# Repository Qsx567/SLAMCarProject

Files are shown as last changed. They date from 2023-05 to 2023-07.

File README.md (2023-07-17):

# SLAMCarProject
### 本项目为我设计的移动SLAM机器人，命名为： <font face="Times New Roman">Q-Robot</font>
<div align="center">
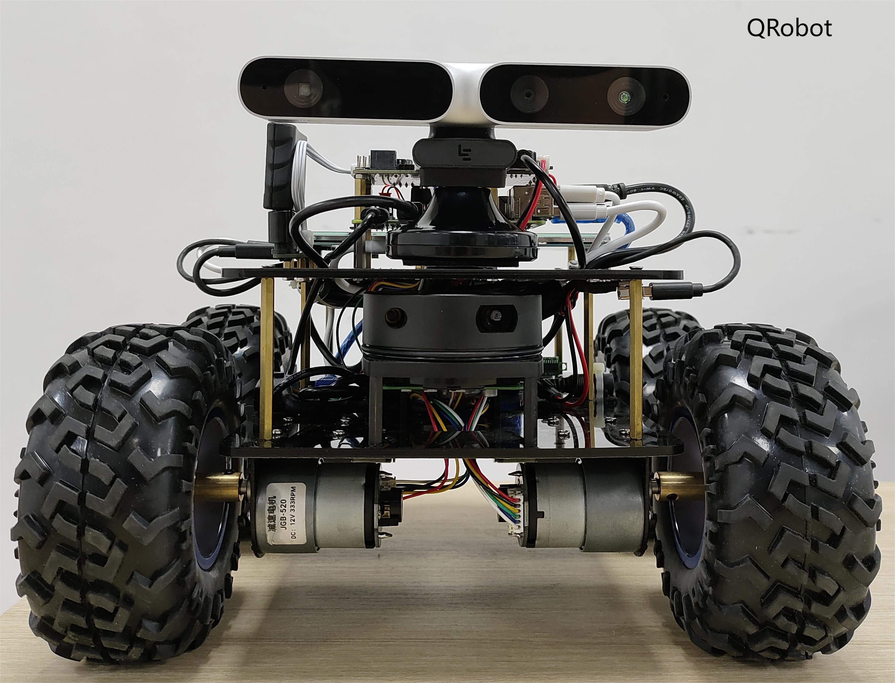
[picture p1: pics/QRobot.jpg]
    <br>
    <font color=#a0a0a0 size=2> 第一层亚克力板图纸</font>
</div>
- 机器人底盘控制器：**STM32F103RCT6**
- 上层控制器：**树莓派4B**
- 传感器：
  - 思岚A1激光雷达
  - Orbbec Astra Pro RGB-D相机
  - 高精度9轴惯导模块N100
  - PS2遥控器
  - wheeltec手柄
- 软件：
  - STM32CubeMX 6.7.0
  - Keil 5.29.0
  - 立创EDA
  - CAD迷你画图

## 一、机器人底盘（亚克力板图纸）
- 总共包括两个文件(plate->plate1.dwg/plate2.dwg)
  - 第一层亚克力板图纸（可放置520电机、锂电池、思岚A1激光雷达/串口板）
  - 第二层亚克力板图纸（可放置Orbbec Astra Pro RGB-D相机、树莓派4B、STM32控制板、PS2遥控器接收器、7寸的显示屏）

<div align="center">
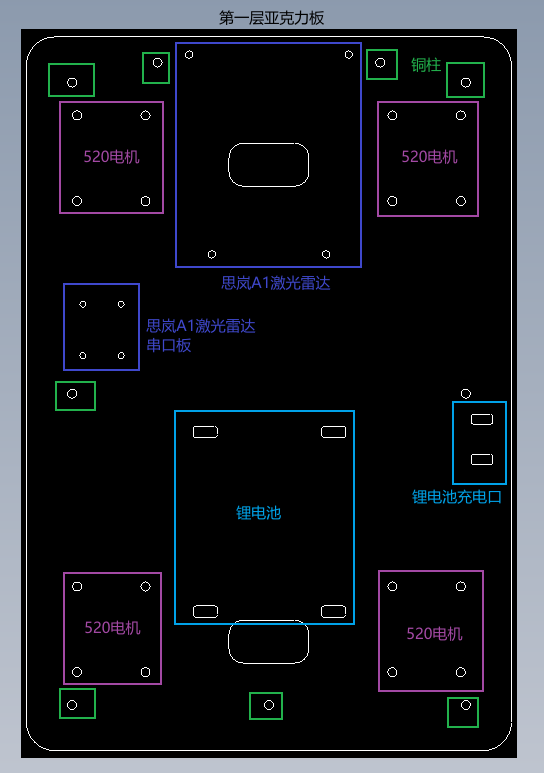
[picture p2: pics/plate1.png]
    <br>
    <font color=#a0a0a0 size=2> 第一层亚克力板图纸</font>
</div>

<div align="center">
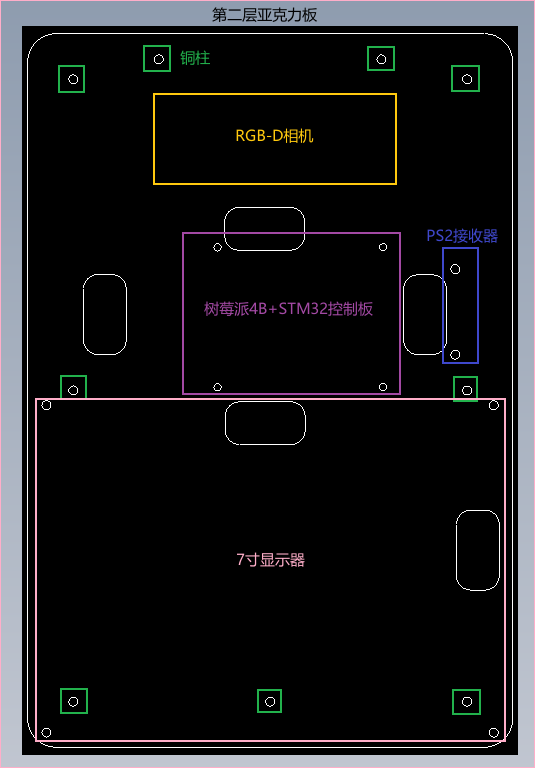
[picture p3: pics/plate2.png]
    <br>
    <font color=#a0a0a0 size=2> 第二层亚克力板图纸</font>
</div>

## 二、机器人底盘控制器原理图

<div align="center">
    <br>
    <font color=#a0a0a0 size=2> 基于SMT32F103RCT6的控制器原理图</font>
</div>

## 三、机器人底盘控制器PCB图

<div align="center">
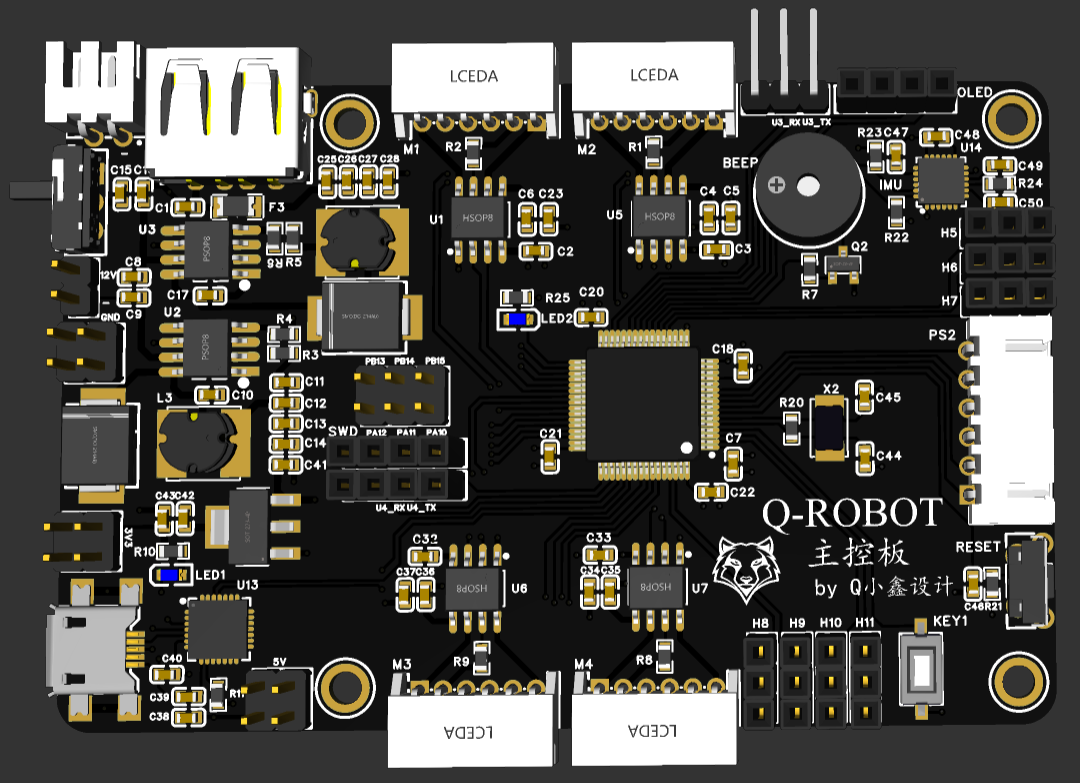
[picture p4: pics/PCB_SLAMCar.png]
    <br>
    <font color=#a0a0a0 size=2> 基于SMT32F103RCT6的控制器PCB图</font>
</div>

## 四、机器人底盘控制器--> STM32
- 电机控制（motor）:TIM5/TIM8
  - Motor1：TIM8_CH1/TIM8_CH2
  - Motor2：TIM5_CH3/TIM5_CH4
  - Motor3：TIM8_CH3/TIM8_CH4
  - Motor4：TIM5_CH1/TIM8_CH2
- 编码器（Encoder）：TIM1/TIM2/TIM3/TIM4
  - Encoder1:TIM1
  - Encoder2:TIM2
  - Encoder3:TIM3
  - Encoder4:TIM4
- PS2遥控器
  - PC0 ->Input    PS2_DAT
  - PC1 ->Output   PS2_COM
  - PC2 ->Output   PS2_ATT
  - PC3 ->OutPut   PS2_CLK
- 串口（UART5）
  - PD2  --> U5_RX
  - PC12 --> U5_TX
- MPU6050（IIC）
  - MPU6050_SDA：PC4
  - MPU6050_SCL：PC5
## 五、ROS相关教程
- 1.使用思岚A1激光雷达
  - 链接: [ROS下使用激光雷达](https://blog.csdn.net/qq_42108414/article/details/121065197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)
- 2.使用Wheeltec N100惯性模块
  - 链接: [ROS下使用N100模块](https://qiushuxin.blog.csdn.net/article/details/130932265)
- 3.使用乐视深度相机LeTMC-520
  - 链接: [ROS下使用乐视深度相机LeTMC-520](https://qiushuxin.blog.csdn.net/article/details/130940896)

已完成情况：
- [x]  添加电机控制（PWM）相关代码
- [x]  添加编码器数据的采集以及转化为速度m/s
- [x]  添加机器人运动模型（四轮模型）运动学逆解
- [x]  添加PID控制算法（增量式） 
- [x]  添加PS2遥控器相关代码
- [x]  添加MPU6050驱动代码，可获取加速度原始值和角速度原始值
- [x]  添加将底层控制数据通过串口发送给ROS端
- [x]  新增FreeRTOS功能，后续只修改维护QRobot_FreeRTOS，基本功能和无OS版本一致，不同之处只是一些逻辑方面
- [x]  添加OLED驱动程序
- [x]  增加思岚A1激光雷达驱动代码
- [x]  增加N100惯性导航模块驱动代码 
- [x]  增加乐视深度相机LeTMC-520驱动代码  
- [x]  增加wheeltec手柄的驱动代码
- [x]  增加STM32和ROS串口通信代码
- [x]  增加PID动态调参代码

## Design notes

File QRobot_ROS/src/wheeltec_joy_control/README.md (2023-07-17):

# 轮趣的PS2遥控器使用方法

## 1、查看输入
```
ls /dev/input
```

## 2、测试
```
sudo apt-get install joystick
sudo jstest /dev/input/js0
```

## 3、编译功能包
```
catkin_make -DCATKIN_WHITELIST_PACKAGES="wheeltec_joy_control"
roslaunch wheeltec_joy joy_data.launch
```

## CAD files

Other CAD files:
plate/plate1.dwg
plate/plate2.dwg

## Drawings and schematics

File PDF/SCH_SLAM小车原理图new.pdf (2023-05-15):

## 电机/编码器接口

## 晶振电路

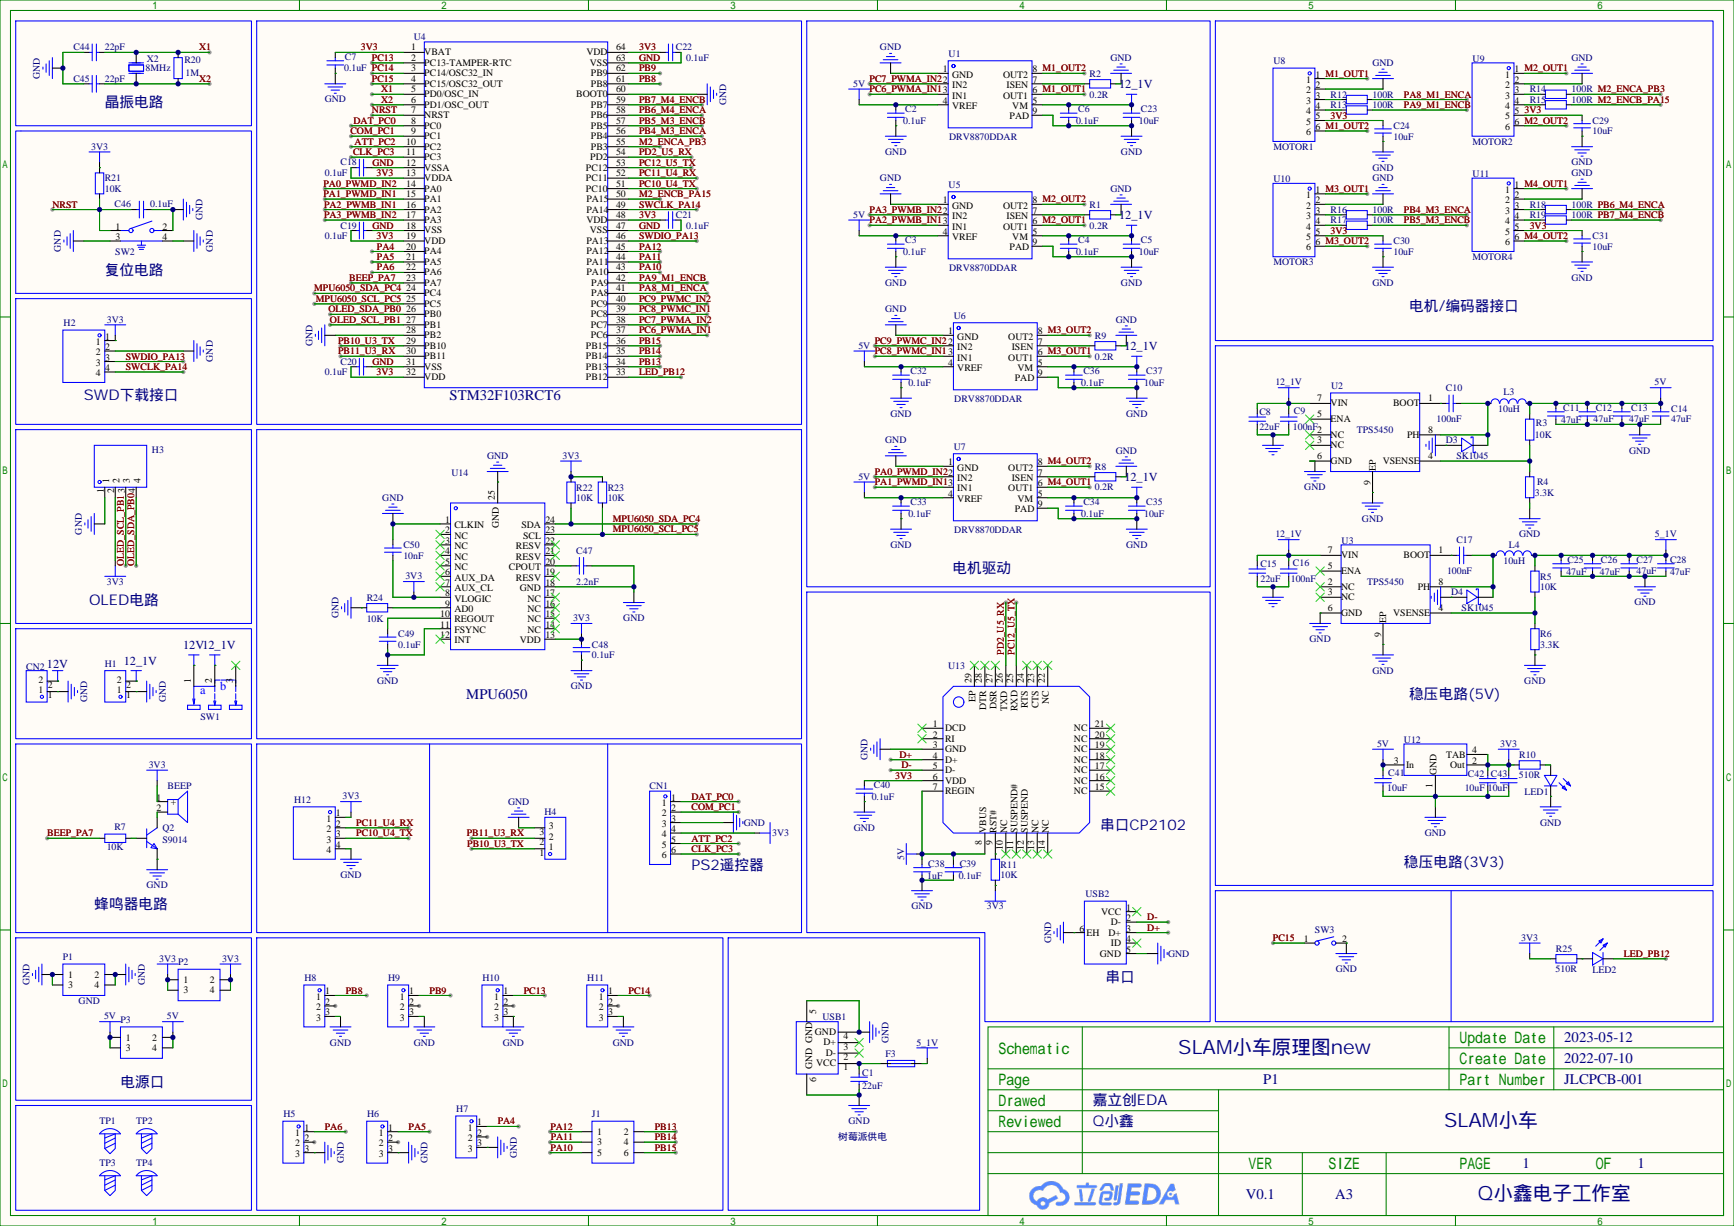
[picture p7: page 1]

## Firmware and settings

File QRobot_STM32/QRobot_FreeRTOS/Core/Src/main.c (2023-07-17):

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
/* Includes ------------------------------------------------------------------*/
#include "main.h"
#include "cmsis_os.h"
#include "tim.h"
#include "usart.h"
#include "gpio.h"


void SystemClock_Config(void);
void MX_FREERTOS_Init(void);
/**
  * @brief  The application entry point.
  * @retval int
  */
int main(void)
{
  /* MCU Configuration--------------------------------------------------------*/

  /* Reset of all peripherals, Initializes the Flash interface and the Systick. */
  HAL_Init();

  /* Configure the system clock */
  SystemClock_Config();

  /* Initialize all configured peripherals */
  MX_GPIO_Init();
  MX_TIM5_Init();
  MX_TIM8_Init();
  MX_TIM1_Init();
  MX_TIM2_Init();
  MX_TIM3_Init();
  MX_TIM4_Init();
  MX_UART5_Init();
  /* USER CODE BEGIN 2 */
	
	OLED_Init();//OLED初始化
	
//	OLED_Refresh();
	
	PS2_Init(); //PS2手柄初始化
	MPU6050_Init(); // MPU6050初始化
	// 电机PWM，满占空比是7199
	HAL_TIM_PWM_Start(&htim8, TIM_CHANNEL_1); // M1_PWMA_1
	HAL_TIM_PWM_Start(&htim8, TIM_CHANNEL_2); // M1_PWMA_2
	HAL_TIM_PWM_Start(&htim8, TIM_CHANNEL_3); // M3_PWMA_1
	HAL_TIM_PWM_Start(&htim8, TIM_CHANNEL_4); // M3_PWMA_2
	
	HAL_TIM_PWM_Start(&htim5, TIM_CHANNEL_1); // M4_PWMA_1
	HAL_TIM_PWM_Start(&htim5, TIM_CHANNEL_2); // M4_PWMA_2
	HAL_TIM_PWM_Start(&htim5, TIM_CHANNEL_3); // M2_PWMA_1
	HAL_TIM_PWM_Start(&htim5, TIM_CHANNEL_4); // M2_PWMA_2
	
	// 编码器
	HAL_TIM_Encoder_Start(&htim1,TIM_CHANNEL_ALL); // M1_ENC
	HAL_TIM_Encoder_Start(&htim2,TIM_CHANNEL_ALL); // M2_ENC
	HAL_TIM_Encoder_Start(&htim3,TIM_CHANNEL_ALL); // M3_ENC
	HAL_TIM_Encoder_Start(&htim4,TIM_CHANNEL_ALL); // M4_ENC
	
	// 串口
	HAL_UART_Receive_IT(&huart5,(void *)&uart5_rxbuff,1);
  /* USER CODE END 2 */

  /* Call init function for freertos objects (in freertos.c) */
  MX_FREERTOS_Init();

  /* Start scheduler */
  osKernelStart();

  /* We should never get here as control is now taken by the scheduler */
  /* Infinite loop */
  /* USER CODE BEGIN WHILE */
  while (1)
  {

		
		
    /* USER CODE END WHILE */

    /* USER CODE BEGIN 3 */
  }
  /* USER CODE END 3 */
}

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
/**
  * @brief  Period elapsed callback in non blocking mode
  * @note   This function is called  when TIM6 interrupt took place, inside
  * HAL_TIM_IRQHandler(). It makes a direct call to HAL_IncTick() to increment
  * a global variable "uwTick" used as application time base.
  * @param  htim : TIM handle
  * @retval None
  */
void HAL_TIM_PeriodElapsedCallback(TIM_HandleTypeDef *htim)
{
  if (htim->Instance == TIM6) {
    HAL_IncTick();
  }
}

/**
  * @brief  This function is executed in case of error occurrence.
  * @retval None
  */
void Error_Handler(void)
{
  /* USER CODE BEGIN Error_Handler_Debug */
  /* User can add his own implementation to report the HAL error return state */
  __disable_irq();
  while (1)
  {
  }
  /* USER CODE END Error_Handler_Debug */
}

#ifdef  USE_FULL_ASSERT
/**
  * @brief  Reports the name of the source file and the source line number
  *         where the assert_param error has occurred.
  * @param  file: pointer to the source file name
  * @param  line: assert_param error line source number
  * @retval None
  */
void assert_failed(uint8_t *file, uint32_t line)
{
  /* USER CODE BEGIN 6 */
  /* User can add his own implementation to report the file name and line number,
     ex: printf("Wrong parameters value: file %s on line %d\r\n", file, line) */
  /* USER CODE END 6 */
}
#endif /* USE_FULL_ASSERT */

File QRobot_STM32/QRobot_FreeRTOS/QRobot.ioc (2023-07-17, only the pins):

Mcu.UserName=STM32F103RCTx
PA0-WKUP.Signal=S_TIM5_CH1
PA1.Signal=S_TIM5_CH2
PA13.Signal=SYS_JTMS-SWDIO
PA14.Signal=SYS_JTCK-SWCLK
PA15.Signal=S_TIM2_CH1_ETR
PA2.Signal=S_TIM5_CH3
PA3.Signal=S_TIM5_CH4
PA7.GPIO_Label=BEEP
PA7.Signal=GPIO_Output
PA8.Signal=S_TIM1_CH1
PA9.Signal=S_TIM1_CH2
PB0.GPIO_Label=OLED_SDA
PB0.Signal=GPIO_Output
PB1.GPIO_Label=OLED_SCL
PB1.Signal=GPIO_Output
PB12.GPIO_Label=LED
PB12.Signal=GPIO_Output
PB3.Signal=S_TIM2_CH2
PB4.Signal=S_TIM3_CH1
PB5.Signal=S_TIM3_CH2
PB6.Signal=S_TIM4_CH1
PB7.Signal=S_TIM4_CH2
PC0.GPIO_Label=PS2_DAT
PC0.Signal=GPIO_Input
PC1.GPIO_Label=PS2_COM
PC1.Signal=GPIO_Output
PC12.Signal=UART5_TX
PC15-OSC32_OUT.GPIO_Label=KEY
PC15-OSC32_OUT.Signal=GPIO_Input
PC2.GPIO_Label=PS2_ATT
PC2.Signal=GPIO_Output
PC3.GPIO_Label=PS2_CLK
PC3.Signal=GPIO_Output
PC4.GPIO_Label=MPU6050_SDA
PC4.Signal=GPIO_Output
PC5.GPIO_Label=MPU6050_SCL
PC5.Signal=GPIO_Output
PC6.Signal=S_TIM8_CH1
PC7.Signal=S_TIM8_CH2
PC8.Signal=S_TIM8_CH3
PC9.Signal=S_TIM8_CH4
PD0-OSC_IN.Signal=RCC_OSC_IN
PD1-OSC_OUT.Signal=RCC_OSC_OUT
PD2.Signal=UART5_RX

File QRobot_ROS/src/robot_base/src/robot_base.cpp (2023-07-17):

#include "robot_base.h"

using namespace std;

float Robot_base::KP = 0;
float Robot_base::KI = 0;
float Robot_base::KD = 0;

// 构造函数
Robot_base::Robot_base()
{
    // 清空接发数据
    memset(&Reciver_Str,0,sizeof(Reciver_Str));
    memset(&Send_Str,0,sizeof(Send_Str));
    x = y = th = vx = vth = dt = 0.0;   

    //发送串口的包头和包尾
    Send_Str.Sensor_str.Header = RECIVER_DATA_HEADER;
    Send_Str.Sensor_str.End = RECIVER_DATA_END;
 
    // 加载串口参数
    nh.param<std::string>("serial/usart_port", this->usart_port, "/dev/ttyUSB0"); // 设置串口端口
    nh.param<int>("serial/baud_rate", this->baud_rate, 115200); // 设置波特率

    // 加载PID参数
    nh.param<float>("PID/KP", Robot_base::KP, 0.0);
    nh.param<float>("PID/KI", Robot_base::KI, 0.0);
    nh.param<float>("PID/KD", Robot_base::KD, 0.0);
    ROS_INFO("KP KI KD = [%f,%f,%f]",Robot_base::KP,Robot_base::KI,Robot_base::KD);
    // 发布话题
    this->moto_pub = nh.advertise<std_msgs::Float32MultiArray>("/robot/MotoEnder",30);
    this->odom_pub = nh.advertise<nav_msgs::Odometry>("odom",50);

    // 订阅话题
    this->cmd_vel_sub = nh.subscribe("/cmd_vel", 100, &Robot_base::cmd_velCallback, this);


    // 创建PID动态参数服务器
    // f = boost::bind(&Robot_base::dynamicParamCallback,_1);
    // server.setCallback(f);
    


    // 打开串口
    try{
        Robot_serial.setPort(this->usart_port);
        Robot_serial.setBaudrate(this->baud_rate);
        serial::Timeout to = serial::Timeout::simpleTimeout(1000);//设置串口超时时间
        Robot_serial.setTimeout(to);
        Robot_serial.open();//打开串口
    }
    catch(serial::IOException &e){
        ROS_INFO_STREAM("Failed to open port ");
    }
    if(Robot_serial.isOpen()){
        ROS_INFO_STREAM("Serial Port initialized!");
    }
    else{
        ROS_INFO_STREAM("Failed to open port ");
    }


}

Robot_base::~Robot_base()
{
    Robot_serial.close();//关闭串口
    cout << "over!!!" <<endl;
}

// 串口读取函数`
bool Robot_base::ReadUart()
{
    unsigned char CheckSumBuffer[1]; 
    Robot_serial.read(Reciver_Str.buffer,sizeof(Reciver_Str.buffer));
    if(Reciver_Str.Sensor_str.Header == RECIVER_DATA_HEADER){
        if(Reciver_Str.Sensor_str.End == RECIVER_DATA_END){
            
            // 获得机器人的速度值
            this->vx  = Reciver_Str.Sensor_str.X_speed;
            this->vth = Reciver_Str.Sensor_str.Z_speed;

            // 获得加速度和角速度值
            MPU6050.linear_acceleration.x = Reciver_Str.Sensor_str.Accelerometer.X_data / ACCELEROMETER;
            MPU6050.linear_acceleration.y = Reciver_Str.Sensor_str.Accelerometer.Y_data / ACCELEROMETER;
            MPU6050.linear_acceleration.z = Reciver_Str.Sensor_str.Accelerometer.Z_data / ACCELEROMETER;

            MPU6050.angular_velocity.x = Reciver_Str.Sensor_str.Gyroscope.X_data * GYROSCOPE_RADIAN;
            MPU6050.angular_velocity.y = Reciver_Str.Sensor_str.Gyroscope.Y_data * GYROSCOPE_RADIAN;
            MPU6050.angular_velocity.z = Reciver_Str.Sensor_str.Gyroscope.Z_data * GYROSCOPE_RADIAN;

            return true;
        }
    }
    //读取空字节防止卡死
    Robot_serial.read(CheckSumBuffer,sizeof(CheckSumBuffer));
    return false;
}

// 发布编码器速度值话题
void Robot_base::PublisherMotoEncoder()
{
    //M1
    Moto_Str.data.push_back(Reciver_Str.Sensor_str.MotoStr[0].Moto_CurrentSpeed);
    Moto_Str.data.push_back(Reciver_Str.Sensor_str.MotoStr[0].Moto_TargetSpeed);

    //M2
    Moto_Str.data.push_back(Reciver_Str.Sensor_str.MotoStr[1].Moto_CurrentSpeed);
    Moto_Str.data.push_back(Reciver_Str.Sensor_str.MotoStr[1].Moto_TargetSpeed);

    //M3
    Moto_Str.data.push_back(Reciver_Str.Sensor_str.MotoStr[2].Moto_CurrentSpeed);
    Moto_Str.data.push_back(Reciver_Str.Sensor_str.MotoStr[2].Moto_TargetSpeed);

    //M3
    Moto_Str.data.push_back(Reciver_Str.Sensor_str.MotoStr[3].Moto_CurrentSpeed);
    Moto_Str.data.push_back(Reciver_Str.Sensor_str.MotoStr[3].Moto_TargetSpeed);

    //M4
    Moto_Str.data.push_back(Reciver_Str.Sensor_str.MotoStr[4].Moto_CurrentSpeed);
    Moto_Str.data.push_back(Reciver_Str.Sensor_str.MotoStr[4].Moto_TargetSpeed);

    moto_pub.publish(Moto_Str); // 发布速度
    Moto_Str.data.clear(); // 清空数据
}

void Robot_base::PublisherOdom()
{
    //将yaw角转化为四元数
    geometry_msgs::Quaternion odom_quat = tf::createQuaternionMsgFromYaw(th);

    if (publish_odom){
        geometry_msgs::TransformStamped odom_transformStamped;
        odom_transformStamped.header.stamp = ros::Time::now();//时间戳
        odom_transformStamped.header.frame_id = "odom";
        odom_transformStamped.child_frame_id = this->robot_frame_id;//base_footprint

        //平移x,y,z
        odom_transformStamped.transform.translation.x = x;
        odom_transformStamped.transform.translation.y = y;
        odom_transformStamped.transform.translation.z = 0.0;

        //旋转w,x,y,z 四元数
        odom_transformStamped.transform.rotation = odom_quat;

        //广播TF
        odom_broadcaster.sendTransform(odom_transformStamped);
    }

    // odom的话题消息发布
    nav_msgs::Odometry odom_msg;
    odom_msg.header.stamp = ros::Time::now();//时间戳
    odom_msg.header.frame_id = "odom";
    odom_msg.child_frame_id = this->robot_frame_id;//base_footprint 

    //发布位姿pose消息
    //平移x,y,z
    odom_msg.pose.pose.position.x = x;
    odom_msg.pose.pose.position.y = y;
    odom_msg.pose.pose.position.z = 0.0;

    //旋转w,x,y,z
    odom_msg.pose.pose.orientation = odom_quat;

    //发布速度
    odom_msg.twist.twist.linear.x = this->vx;
    odom_msg.twist.twist.linear.y = 0;
    odom_msg.twist.twist.angular.z = this->th;

    if((this->vx == 0)&&(this->th==0))
    {//当速度为0,说明编码器的误差会比较小，认为编码器的数据更可靠
        memcpy(&odom_msg.pose.covariance,odom_pose_covariance2,sizeof(odom_pose_covariance2));
        memcpy(&odom_msg.twist.covariance,odom_twist_covariance2,sizeof(odom_pose_covariance2));
    }
    else
    {//如果小车的速度非零，考虑到运动中的编码器可能带来的滑动误差，认为imu的数据更可靠
        memcpy(&odom_msg.pose.covariance,odom_pose_covariance,sizeof(odom_pose_covariance));
        memcpy(&odom_msg.twist.covariance,odom_twist_covariance,sizeof(odom_twist_covariance));
    }

    //发布消息
    odom_pub.publish(odom_msg);
}

// 循环函数
void Robot_base::LoopProcess()
{
    this->last_time = ros::Time::now(); // 获取时间
    while(ros::ok()){
        
        //计算时间dt
        this->current_time = ros::Time::now(); // 获取当前时间
        this->dt = (current_time - last_time).toSec(); // 转化为秒为单位
        this->sampleFreq = 1.0f / dt;//采样率

        if (ReadUart()){ // 如果能读取串口成功
            
            // 计算tf和odom
            x +=  vx*cos(th) * dt;
            y +=  vx*sin(th) * dt;
            th += vth * dt;



            PublisherMotoEncoder(); // 发布速度数据


        }




        this->last_time = current_time;  
        ros::spinOnce(); 
    }
}




// 动态调参回调函数
void Robot_base::dynamicParamCallback(robot_base::pidConfig &config)
{
    Robot_base::KP = config.KP;
    Robot_base::KI = config.KI;
    Robot_base::KD = config.KD;

    ROS_INFO("KP KI KD = [%f,%f,%f]",Robot_base::KP,Robot_base::KI,Robot_base::KD);
}
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

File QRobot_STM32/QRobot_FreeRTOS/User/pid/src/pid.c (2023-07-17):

#include "pid.h"


// 增量式PID
// pwm+=Kp[e（k）-e(k-1)]+Ki*e(k)+Kd[e(k)-2e(k-1)+e(k-2)
// 只使用PI控制

float KP = 800;
float KI = 200;
float KD = 0;


float PID_Incremental(_Moto *MOTOR)
{
	float Error = 0; 		// 当前误差
	float P_Error = 0; 	// P项的误差
	float I_Error = 0; 	// I项的误差
	float D_Error = 0; 	// D项的误差
	
	Error = MOTOR->Target_Speed - MOTOR->Current_Speed; // 目标速度-当前速度
	
	// 计算PID的误差
	P_Error = Error - MOTOR->L_Error; // 当前误差 - 上次误差
	I_Error = Error; // 当前误差
	D_Error = Error - 2*MOTOR->L_Error + MOTOR->LL_Error; // 当前误差-2*上次误差+上上次误差
	
	// 计算最终输出的PWM值
	MOTOR->PWM_OUT += (KP * P_Error + KI * I_Error + KD * D_Error);
	
	// 更新误差
	MOTOR->LL_Error = MOTOR->L_Error;
	MOTOR->L_Error = Error;
	
	// 限幅
	if(MOTOR->PWM_OUT > PWM_OUT_LIMT)  MOTOR->PWM_OUT = PWM_OUT_LIMT;
	if(MOTOR->PWM_OUT < -PWM_OUT_LIMT) MOTOR->PWM_OUT = -PWM_OUT_LIMT;
	
	return MOTOR->PWM_OUT;
}

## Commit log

2023-05-12 初步构建STM32环境，并配置LED/BEEP/Key文件
2023-05-13 更新底盘电机控制代码
2023-05-14 更新编码器相关代码
2023-05-14 更新机器人运动模型以及PID控制代码
2023-05-14 更新README
2023-05-14 新增PS2遥控器相关代码
2023-05-15 添加串口收发数据
2023-05-15 更新plate1
2023-05-15 更新机器人底盘亚克力板图纸
    [plate1.dwg, plate2.dwg]
2023-05-15 更新plate2
2023-05-15 修改README
2023-05-15 添加机器人控制器原理图
2023-05-15 修改gitignore文件
2023-05-15 修改README文件
2023-05-15 更改README
2023-05-15 添加PCB图
2023-05-15 添加MPU6050相关代码
2023-05-15 新增FreeRTOS功能
2023-05-15 修改gitignore
2023-05-24 添加思岚A1驱动代码
2023-05-29 增加N100驱动代码
2023-05-29 修改READNE文件
2023-05-30 添加astra_pro驱动代码
    [Astra.cfg, UVCCamera.cfg]
2023-05-30 修改思岚A1launch文件以及udev文件
2023-06-22 更新电机驱动程序以及编码器驱动程序
2023-06-22 增加QRobot实物图
2023-06-23 修改串口文件
2023-06-23 修改freerots为静态创建任务
2023-06-23 增加OLED驱动代码
2023-07-17 修改了部分代码
2023-07-17 新增wheeltec的手柄驱动代码
2023-07-17 新增底盘控制代码
    [pid.cfg, robot_base.yaml]

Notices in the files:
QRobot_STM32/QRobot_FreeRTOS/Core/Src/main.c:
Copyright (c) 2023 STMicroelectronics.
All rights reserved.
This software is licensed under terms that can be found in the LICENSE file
